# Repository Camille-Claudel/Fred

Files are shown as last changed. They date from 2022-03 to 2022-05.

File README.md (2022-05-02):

# Introduction

https://user-images.githubusercontent.com/80780126/160250190-fc86b303-d6f0-4ee5-a104-70d04af33471.mp4 

Ce projet a pour but la création d'une main robotique, en s'inspirant du fonctionnement d'une main humaine.

## Objectifs
L'objectif principal est de pouvoir plier ou déplier complètement chacun des doigts, indépendamment les uns des autres. On peut alors implémenter différents gestes de la main, et par exemple programmer un jeu de pierre-feuille-ciseaux. Les objectifs secondaires incluent la capacité à attraper des objets, et la capacité à plier les doigts dans des positions intermédiaires (ce qui permettrait notamment de réguler la vitesse à laquelle les doigts se plient ou se déplient). À plus long terme, le projet pourrait évoluer pour permettre des mouvements plus complexes, par exemple en contrôlant chaque phalange de manière indépendante ou en permettant des mouvements latéraux.

# Principe de fonctionnement
Chez l'homme, les muscles qui permettent de plier les doigts ne se trouvent pas dans les doigts: la flexion est contrôlée par des tendons, sur lesquels tirent des muscles situés dans l'avant-bras (en particulier le muscle fléchisseur profond des doigts).  
Pour chaque phalange, il y a un tendon fléchisseur situé du côté intérieur, et un tendon extenseur situé du côté extérieur. En tirant sur le tendon extenseur, le doigt se déplie, et en tirant sur le tendon fléchisseur il se plie.  
19-06-27-15-40-36_798959289_thumbnail_large2  
De nombreux autres tendons sont présents dans la main, mais ceux-ci sont les plus importants pour notre projet.  
Pour reproduire plus fidèlement une main biologique, il faudrait deux tendons fléchisseurs (et deux moteurs-muscles) pour chaque doigt. Cependant, il est plus simple pour l’instant de se limiter à un seul moteur-muscle et une seule paire de tendons pour chaque doigt.
Pour fermer le doigt, le moteur tourne de manière à tirer sur le tendon fléchisseur et à détendre le tendon extenseur, ce qui plie le doigt. En tournant le moteur dans l’autre sens, le doigt s’ouvre.


# Difficultés rencontrées et solutions apportées
## Choix de l’architecture
Chaque doigt est composé de 3 phalanges identiques (à la taille près), sauf pour le pouce qui n’a que 2 phalanges. Elles sont reliées par des articulations pouvant se plier de 60°. Un tendon passe à l'intérieur des phalanges dans des tubes prévus à cet effet. Les doigts sont attachés à une paume fixe sans fonction mécanique, le pouce étant incliné par rapport aux autres doigts. Les tendons des doigts sont prolongés à travers la paume, et passent par le poignet pour arriver aux moteurs, situés au niveau de l’avant bras. Ces moteurs sont des servomoteurs (capables de s’orienter précisément vers une position entre 0 et 180°), et contrôlés par une carte Arduino.


## Choix des méthodes de fabrication
Les articulations sont constituées de tubes pivotant autour d’un cure-dent, à la manière d’une charnière.  
Les tendons sont des fils de pêche, fins et résistants.  
Les phalanges et le bloc moteur sont des pièces imprimées en 3D en résine, ce qui permet d’avoir une géométrie très complexe et très précise.  
La paume est imprimée en 3D en PLA, ce qui est moins précis mais permet d’imprimer des pièces plus grandes.

## Résistance
Avec notre premier prototype, la force nécessaire pour plier et déplier le doigt était beaucoup trop importante. Afin d'y remédier, nous avons éloigné les tendons de l'axe central. Ainsi, le couple exercé sur les phalanges est maximisé, ce qui diminue la force nécessaire pour plier ou déplier le doigt.  
De plus, nous avons creusé les phalanges, pour minimiser la longueur des tubes dans lesquels coulissent les tendons. Cela a eu pour effet de rendre la flexion et l'extension du doigt beaucoup plus faciles. Notre interprétation est que les frottements sont importants à l'intérieur du tube, et donc que creuser les phalanges a permis de limiter ces frottements.  
  
un des premiers prototypes, non creusé (gauche) VS version creusée (droite):


## Asymétrie
Nous avons remarqué qu'avec le prototype que nous avions à ce stade, il était impossible de tendre les tendons correctement: s'ils étaient tendus quand le doigt était déplié, le tendon extenseur était détendu quand le doigt était plié. Nous avons réalisé que cela était dû à l'éloignement des tendons à l'axe central: ils étaient jusque là placés à la même distance, mais en réalité le tendon fléchisseur aurait dû être moins éloigné d'un facteur cos(30°) pour que la distance dont le fil doit être rétracté (notée ΔL sur le schéma) soit la même des deux côtés.  


## Tension
Tendre les tendons s'est révélé être plus difficile que prévu. En effet, il est très difficile de coller le fil au moteur en le maintenant tendu. Nous avons donc décidé de mettre en place un système pour pouvoir régler la position du moteur après avoir collé les fils. Ainsi, si les fils ne sont pas tendus après les avoir attachés, on peut reculer le moteur, ce qui a pour effet de tendre les fils. Pour pouvoir régler la position du moteur, on l'attache à un chariot monté sur des vis. En serrant les vis, on peut alors reculer le moteur.  


## Rigidité
il y avait beaucoup de jeu au niveau du bloc moteur, ce qui pose une fois de plus un problème pour tendre les fils. En effet, la flexibilité de la résine permettait à la pièce de se plier. Pour y remédier, nous avons adapté la géométrie de la pièce pour permettre l'insertion de deux tiges en aluminium assurant le parallélisme entre la partie droite et gauche du bloc moteur et la rigidité de l'ensemble.  


## Complexité du montage
Bien que le branchement des servomoteurs soit relativement simple en principe, le montage final est composé d'au moins une vingtaine de fils, ce qui peut rapidement rendre le circuit difficile à comprendre, d'autant plus que la platine que nous utilisions était trop petite.En particulier, il n'est pas pratique de diagnostiquer une erreur dans un tel montage.

Pour réduire le nombre de fils nécessaires, nous avons alors conçu et fabriqué un circuit imprimé. On utilise pour cela une plaque en plastique recouverte d'une couche de cuivre, sur laquelle on imprime en 3D (en résine) le tracé du circuit voulu. Le motif ainsi formé servira de masque. Ensuite, on dissout le cuivre non masqué avec une solution d'acide acétique (vinaigre), de peroxyde d'hydrogène (eau oxygénée), et de chlorure de sodium (sel de table). On obtient alors un circuit imprimé sur lequel on soude des connecteurs qui permettent de brancher les servomoteurs directement, sans passer par un fil.



## Résultat final
Voici une vidéo de la naissance de Fred le 19 mars vers minuit 30:  

https://user-images.githubusercontent.com/80780126/160250168-33cd308e-4ac8-43aa-821d-4a71da2489f3.mp4

Et voici deux vidéos de Fred aux portes ouvertes du lycée le 19 mars vers 10 heures:

https://user-images.githubusercontent.com/80780126/160250184-eb81a975-74f4-4f95-affd-3359798cb3a0.mp4

https://user-images.githubusercontent.com/80780126/160250190-fc86b303-d6f0-4ee5-a104-70d04af33471.mp4

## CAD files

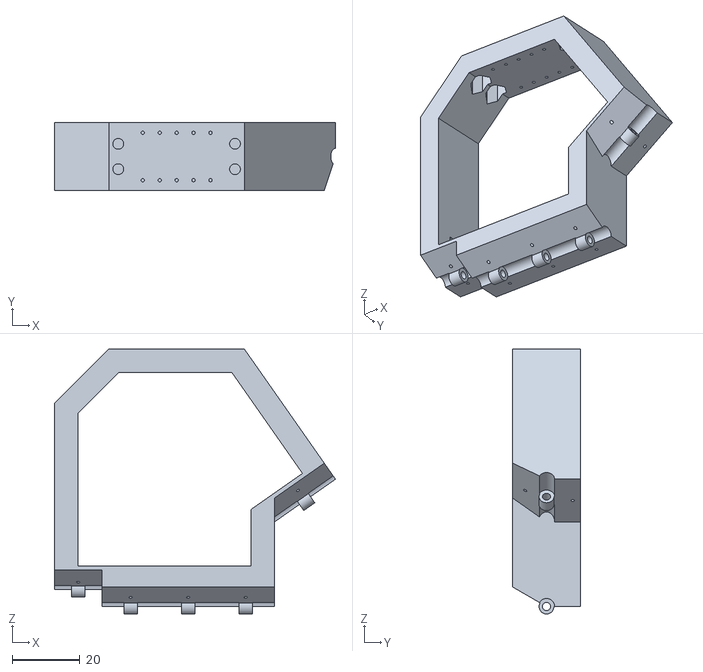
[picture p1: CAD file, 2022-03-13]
STL files/hand/palm.stl
83.0 x 20.0 x 78.3

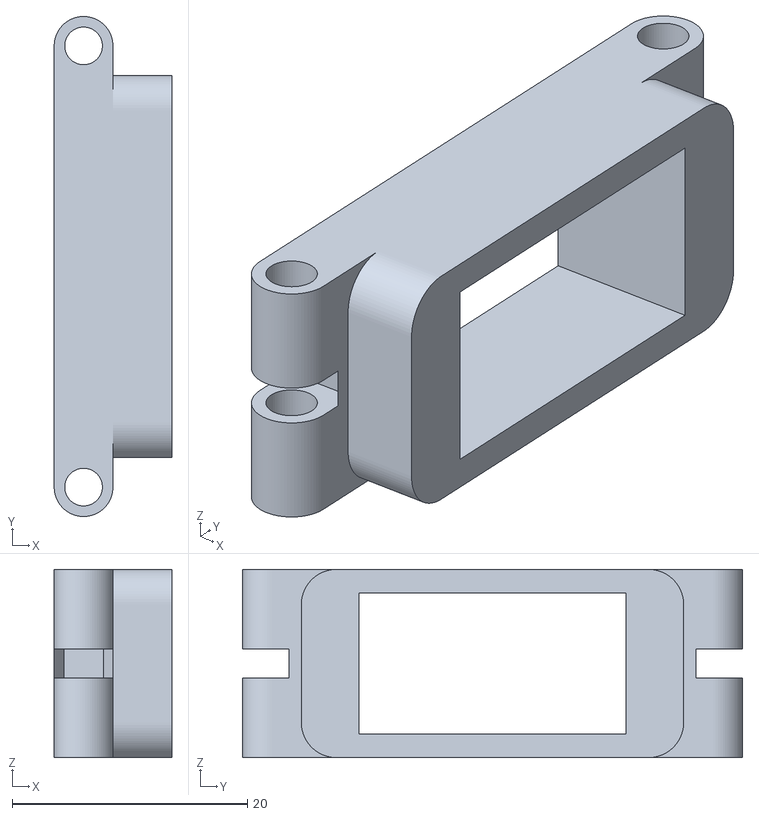
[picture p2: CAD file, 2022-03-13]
STL files/motor block/motor slider.stl
10.0 x 42.5 x 16.0

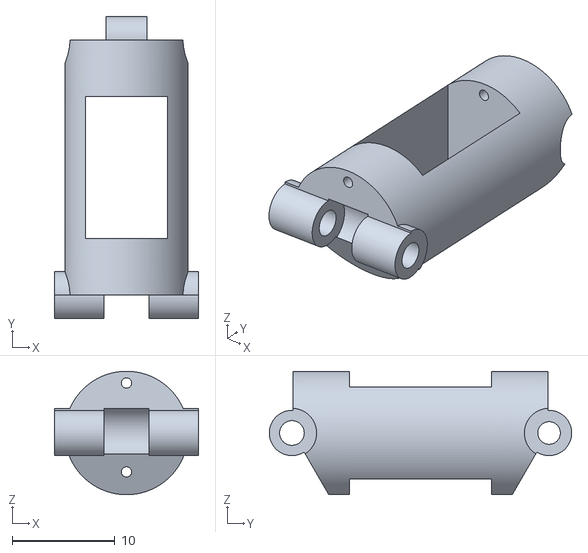
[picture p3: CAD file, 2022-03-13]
STL files/hand/thin phalanx.stl
14.0 x 29.4 x 12.0

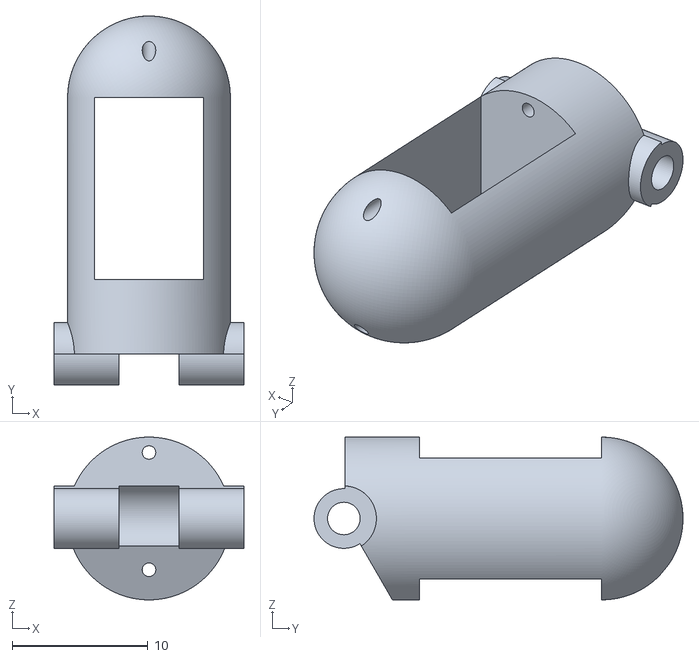
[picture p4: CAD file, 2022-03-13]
STL files/hand/thin extreme phalanx.stl
14.0 x 27.2 x 12.0

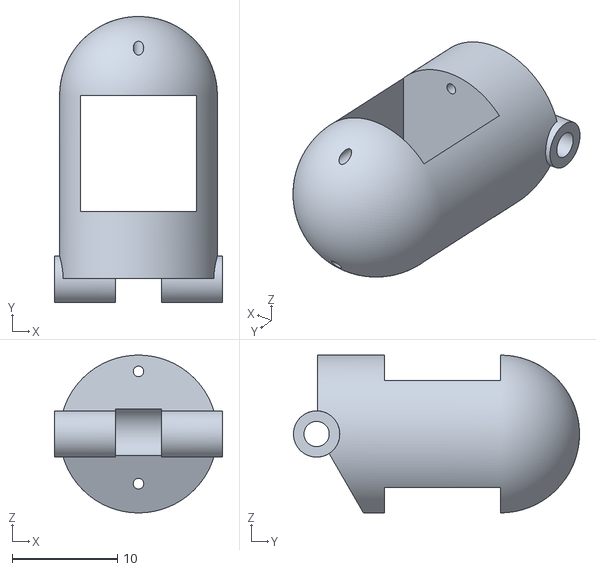
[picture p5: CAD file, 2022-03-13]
STL files/hand/extreme phalanx.stl
16.0 x 27.2 x 15.0

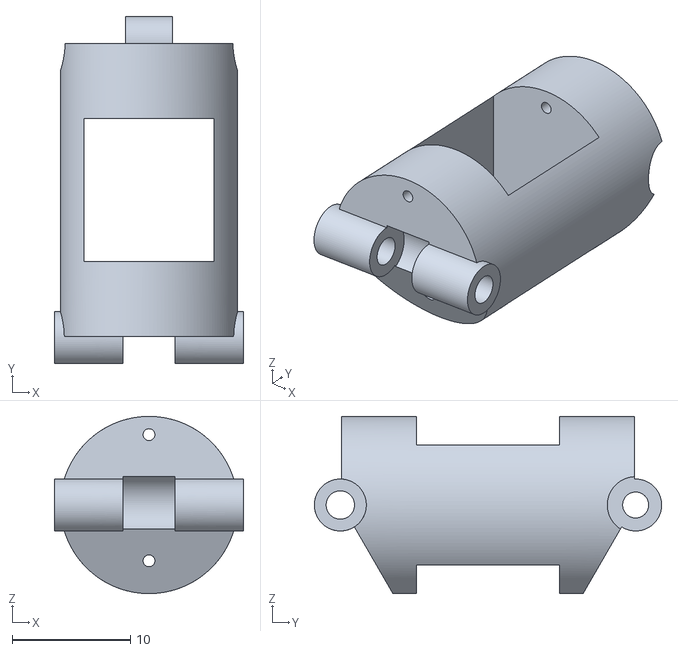
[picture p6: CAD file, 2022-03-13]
STL files/hand/phalanx.stl
16.0 x 29.4 x 15.0

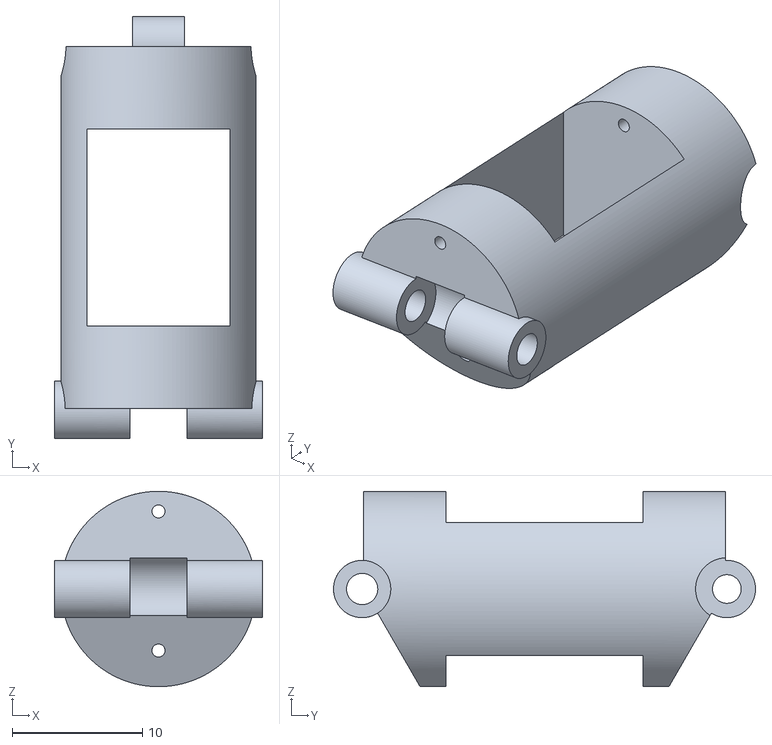
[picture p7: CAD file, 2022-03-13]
STL files/hand/long phalanx.stl
16.0 x 32.4 x 15.0

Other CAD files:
f3d files/engine block.f3d
f3d files/palm.f3d
f3d files/phalanx.f3d

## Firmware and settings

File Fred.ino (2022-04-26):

#include <Servo.h>

Servo servos[5];

// be careful, the first 2 must be on the short side of the motor block
// and the last 3 on the long side
int pins[5] = {3,5,6,9,10};

int bounds[5][2] = { // closed and open position of each finger
  {30,100}, // short 1
  {30,130}, // short 2
  {30,120}, // long 1
  {20,120}, // long 2
  {30,110}  // long 3
};

void doPosition(String code)
{
  /*
  interprets a sequence of 0s and 1s as positions for each finger
  for example "11011" is:
    pinky closed
    ring finger closed
    middle finger open
    index finger closed
    thumb closed
  */
  for (int i = 0; i < 2; i++) // short side
  {
    if (code[i] == '0')
    {
      servos[i].write(bounds[i][0]);
    }
    else if (code[i] == '1')
    {
      servos[i].write(bounds[i][1]);
    }
  }
  for (int i = 2; i < 5; i++) // long side
  {
    // angles reversed because the motors of the long side are facing the opposite direction
    if (code[i] == '0')
    {
      servos[i].write(180-bounds[i][0]);
    }
    else if (code[i] == '1')
    {
      servos[i].write(180-bounds[i][1]);
    }
  }
}

void setup() {
  for (int i = 0; i < 5; i++)
  {
    servos[i].attach(pins[i]);
  }
}

void loop() {
  // by default, open and closes the hand with a delay of 1 second
  delay(1000);
  doPosition("00000");
  delay(1000);
  doPosition("11111");
}

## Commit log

2022-03-13 Rename STL files/phalanx/.gitkeep to STL files/hand/.gitkeep
2022-03-13 edit palm
    changed the location of the screws
    [palm.stl]
2022-03-13 edit palm
    [palm.f3d]
2022-03-13 added clearance
    [long bottom.stl, long top.stl, short bottom.stl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]
2022-03-14 added a screw
    [long bottom.stl, long top.stl, short bottom.stl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]
2022-03-14 fix mistake
    [long bottom.stl]
2022-03-17 fix mistake
    yes i know, please stfu
    [long bottom.stl]
2022-03-17 Update README.md
    - added schemas
    - betterified "tension" part
    - added "rigidité" and "complexité du montage" parts
2022-04-26 added comments
    added comments to make the code clearer and deleted the "alternate" bool which didn't really make sense
    [Fred.ino]
